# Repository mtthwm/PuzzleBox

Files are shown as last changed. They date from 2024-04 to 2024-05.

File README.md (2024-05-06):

# About

## Description
This is a project built for our ECE 5780 (Embedded Systems) final project. We built a puzzle box that requires the user to interact with it in novel ways to unlock and reveal the prize inside. 

### Puzzle 1: Knock and Response 

The buzzer plays a common knock rhythm, and the user must respond to finish the rhythm. 
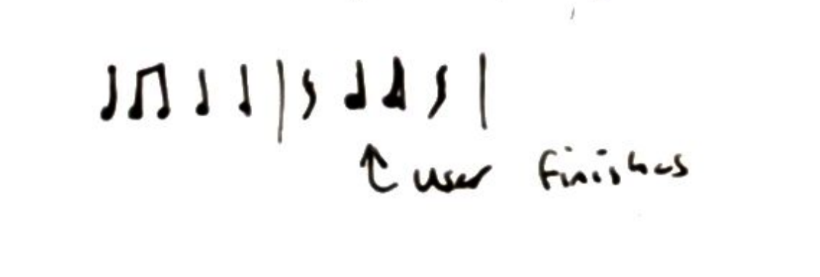
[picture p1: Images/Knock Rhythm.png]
Image of the common door knock rhythm that everyone knows


### Puzzle 2:  

Led on sides of the box lights up, rotate the whole box so the LED points down. Repeat 3 times with a random side each time. 

### Puzzle 3: 

Using multiple photoresistors, a sequence of holes needs to either be lit or covered.  

### Puzzle Completion: 

Using a servo, unlock the box for opening. Puzzle restarts on close. 

## Collaborators
- Matthew Morales
- Daniel Reyna
- Casey Wolfe
- Griffin Rodgers

# Project Setup Instructions

## Assembly
1. Print the box and lid using the provided STL files. Our original design was slightly off, which required us to drill into the box to make room for the servo locking mechanism.
2. Glue LEDs and photoresistors into the holes in the side. Each LED has a 220 Ohm resistor in series, and each photoresistor is part of a voltage divider with a 10k Ohm resistor. Make sure to match up the LEDs which correspond to the photoresistors.
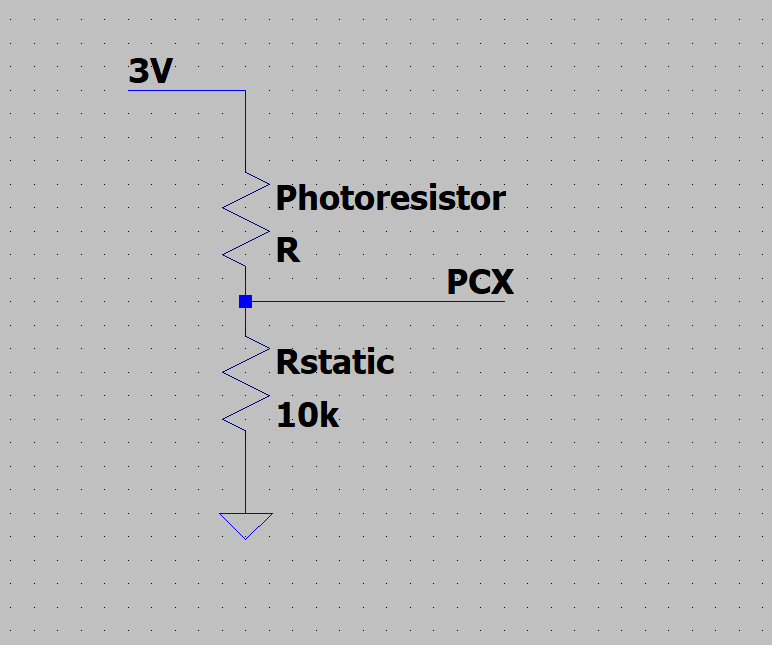
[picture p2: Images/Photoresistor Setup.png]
Photoresistor voltage divider example

3. Attach the piezo resistor to the underside of the lid using hot glue. This seems to cushion the vibrations picked up by the piezo resistor enough to avoid large voltage spikes. As a result, we didn't connect it to a voltage divider.
4. Once the piezo sensor is attached, you may need to use usart to display the values in order to pick a proper voltage threshold for the piezo sensor. It seemed the voltage generated by these sensors varied significantly
5. Open the project in Keil uVision, compile the project, and flash it to your STM32F0 Discovery Kit Board.

## Pins
- I2C:  
  - SCL: PB10 
  - SDA: PB11 

- UART (debug):  
  - TX: PC10 
  - RX: PC11 

- ADC: PC0-3
  - Piezo: PC0 
  - Photoresistors PC3,4,5

- Buzzer: PB5 

- Box-Side LEDs 
   - PA0 -- Top LED 
   - PA1 – Base LED 
   - PA8 – Front LED 
   - PA9 – Back LED 
   - PA10 – Left Side LED
   - PA15 – Right Side LED	 

- Servo: PB3 

# Puzzle Box - Hints & Solution
## Hints (for fun)
Given: Each stage completion (3 total) will be associated with a victory tune, as well as a brief LED light show.

### Hint (1): 
The box plays a near complete tune, no question there; make haste and knock to – to finish it is the burden you bear.

### Hint (2): 
The box has many sides, it is of no surprise; what does the light confide? Rotate to abide?

### Hint(3.1): 
Your final steps await, the box’s prize is in your fate; darkness – you think – may be your friend, but its enemy may tend.

### Hint(3.2):
Thus far you found your tool, you’re on the path; but have you checked if there is a dual?

## Solution
(1) A buzzer plays an incomplete tune. Wait until it finishes. Knock once, wait half a second then knock again. A victory tune will be played
(2) An LED will indicate which side needs to be up. First is bottom, then right side, then top. A victory tune will be played
(3) LEDs will indicate which side’s photoresistor must be interacted with. You must shine a light to the bottom side photoresistor first, followed by the back, followed by both back and top (2 lights required, or 1 shining on both directly)
(4) An extended victory tune is played, followed by a LED lightshow. The box servo unlocks shortly after and can be opened.

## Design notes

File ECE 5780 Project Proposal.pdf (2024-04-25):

## Group Members

Casey Wolfe
Matthew Morales
Griffin Rodgers
Daniel Reyna

## Project Description

We will build a puzzle box that requires the user to interact with it in novel ways to unlock and reveal the prize inside. The box will have a GPS, a knock detector piezo sensor, a gyroscope, and a photo resistor hidden inside. Markings on the outside of the box will guide the user to interact with the various inputs to solve puzzles. A buzzer inside the box and LED indicators will provide active feedback to the user. There will be four puzzles, once all the puzzles are solved a solenoid will unlock the box from inside.
Puzzle ideas include tilting the box to a certain orientation, moving the box a specific distance, knocking on the box in a specific pattern, and shining a light through a small hole in the box.

## Motivation

We chose this project idea because it seemed like a very flexible way to get experience with a lot of different sensors and actuators. We also thought it would be a creative and unique concept to explore, combining both embedded systems and game design. We have selected unconventional user interfaces that use technology to challenge the user to think creatively to solve puzzles.

## Block Diagram

## Hardware Components

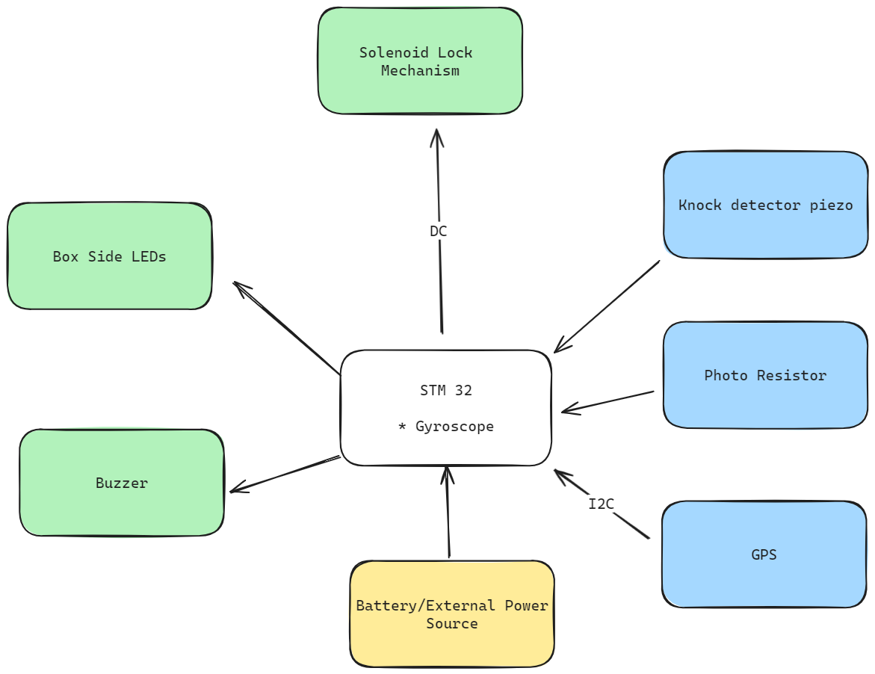
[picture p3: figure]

## Software State Machine

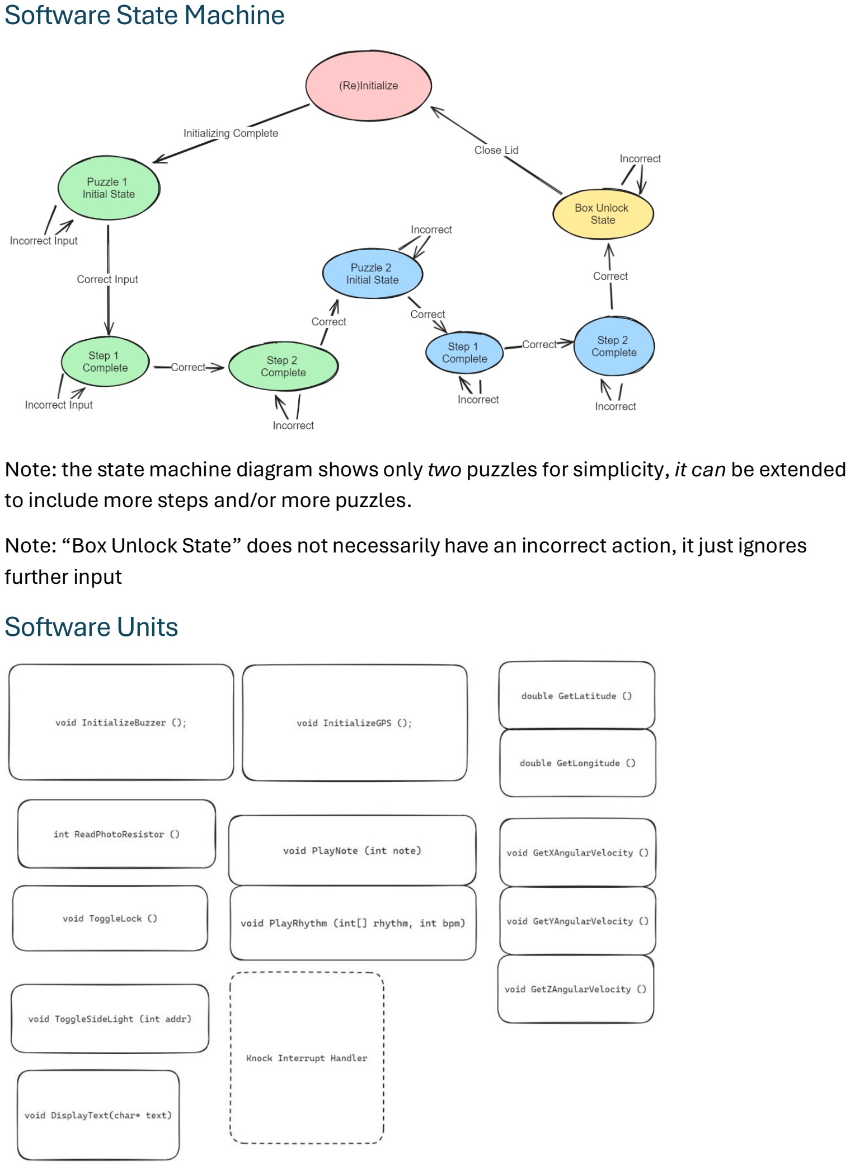
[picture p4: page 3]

Note: the state machine diagram shows only two puzzles for simplicity, it can be extended to include more steps and/or more puzzles.
Note: “Box Unlock State” does not necessarily have an incorrect action, it just ignores further input

## Software Units

## Milestones

## Milestone 1

Primary Goal: Communication with the piezo sensor, and buzzer.

- Buzzer can play a rhythm
- Main loop switch statement for state machine
Secondary Goals:
- Piezo sensor can detect a pattern of taps
- Obtain parts
- Puzzles designed

## Milestone 2

Primary Goal: Communication with accelerometer for rotation puzzle. Main state machine architecture complete.

- Can decide which side is facing down
- We can easily address the side LEDs
- We can randomly turn on an LED Secondary Goals:
- Box design complete
Tasks:
- Piezo
- Detect knocks
- Store knock history
- Buzzer
- Function to play tone for certain time
- Play sequence of tones
- Accelerometer
- Read I2C
- Function to return which side is down

o

## Milestone 3

Primary Goal: Measurement of the photoresistors

- We can detect light/dark/ambient state on each photo resistors
- We can communicate with 5 Photoresistors
- Can rapidly flash LEDs on one side
Secondary Goals:
- Box assembled

## Milestone 4

Primary Goal: Communication with servo to open the lid; Finished puzzle box.

- Can send a lock/unlock signal to the lock mechanism
- Play a fanfare on open
- Can transition to back to play state
Secondary Goals:
- Fully test the project
- Debug/fix any software issues
- Add features if time permits

## Discussion of Risk

One of the biggest risks we have identified with this mini project is the physical design aspects of the puzzle box. We have access to a 3D printer for rapid prototyping of the box, however none of us are particularly experienced in 3D modeling. This risk will be mitigated by dedicating time to learning basic 3D modeling in CAD software.
Another risk is that our team does not include an Electrical Engineer, so we may struggle more with some of the hardware design/implementation aspects of the project. This risk is partially mitigated through having two Computer Engineers on the team; however, Computer Engineers are not as experienced in hardware as an Electrical Engineer would be.

## Pins

I2C:
SCL: B10
SDA: B11
UART (debug):
TX: PC10
RX: PC11
ADC: A pins
Piezo: C0
Photoresistors: PA1-5 and PA7 DMA BUFFER:
PIEZO - [0]
Top Resistor - [1]
Bottom Resistor - [2]
Back Resistor - [3]
Buzzer: PB5

Box-Side LEDs

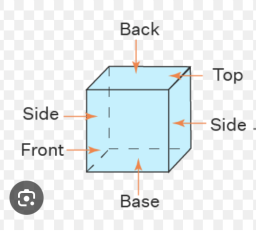
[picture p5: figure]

PA0 -- Top LED
PA1 – Base LED
PA8 – Front LED
PA9 – Back LED

PA10 – Left Side LED
PA15 – Right Side LED
Servo: PB3

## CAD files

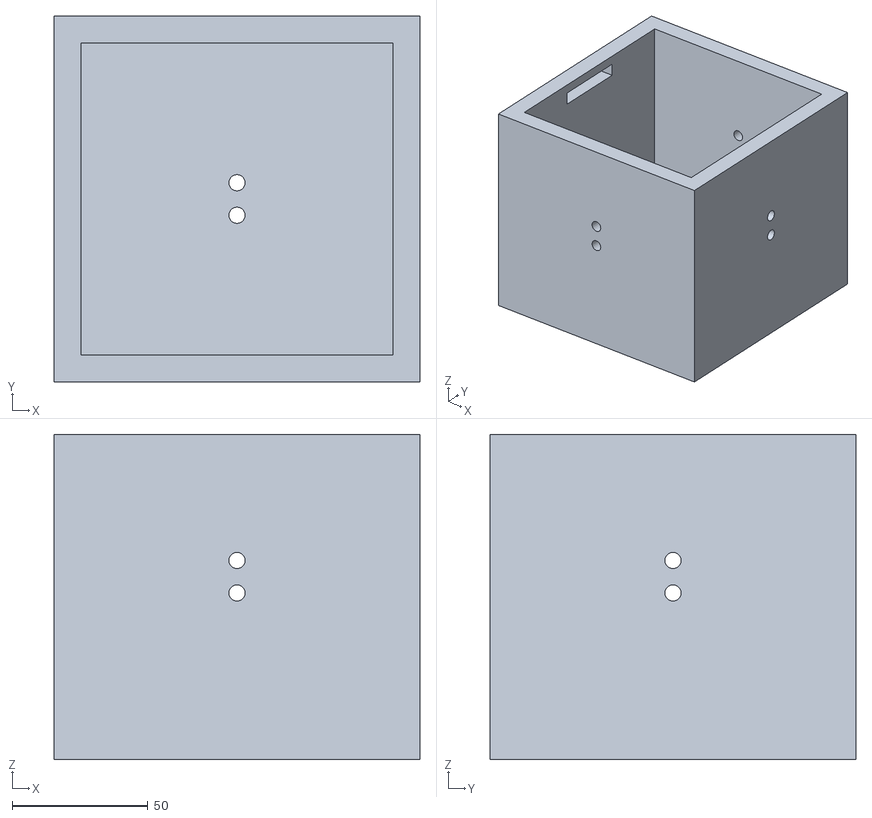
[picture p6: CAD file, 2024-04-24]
Puzzle Box.stl
135.0 x 135.0 x 120.0

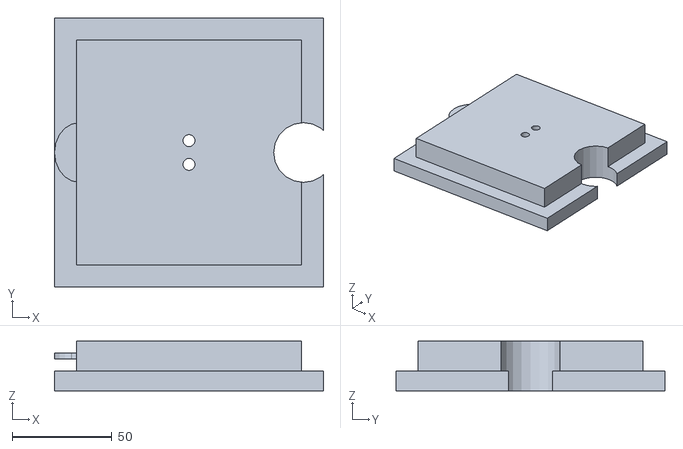
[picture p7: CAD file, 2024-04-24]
Puzzle Box Lid.stl
135.0 x 135.0 x 25.0

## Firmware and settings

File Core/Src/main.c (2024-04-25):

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
/* Includes ------------------------------------------------------------------*/
#include "main.h"

/* USER CODE BEGIN Includes */

#include "servo.h"
#include "accel.h"
#include "adc.h"

/* USER CODE END Includes */

/* USER CODE BEGIN PV */

// Contains values for 3 photoresistors and PIEZO
// [0] contains piezo
// [1] is the top photoresistor
// [2] is the bottom photoresistor
// [3] is the back photoresistor

/* USER CODE END PV */

void SystemClock_Config(void);
/* USER CODE BEGIN 0 */


void victoryBoxLEDs();
void unlock ();

////////////////// UART ////////////////////////////////////////////////////////////////////////
#define RX_BUFF_SIZE 2

static char rx_chars[RX_BUFF_SIZE];
static int rx_i = 0;

/**
	* @brief Configures USART with PC10=RX, PC11=TX
	*/
void config_usart (uint32_t baudrate) {
	// Set the mode of the GPIO pins to use an alternate function
	GPIOC->MODER &= ~(GPIO_MODER_MODER10_Msk);
	GPIOC->MODER &= ~(GPIO_MODER_MODER11_Msk);
	GPIOC->MODER |= (2 << GPIO_MODER_MODER10_Pos);
	GPIOC->MODER |= (2 << GPIO_MODER_MODER11_Pos);

	
	// Set GPIO Pins PC10 and PC11 to use alternate function AF1: USART3
	GPIOC->AFR[1] &= ~GPIO_AFRH_AFSEL10_Msk;
	GPIOC->AFR[1] |= (GPIO_AF1_USART3 << GPIO_AFRH_AFSEL10_Pos); // TX
	GPIOC->AFR[1] &= ~GPIO_AFRH_AFSEL11_Msk;
	GPIOC->AFR[1] |= (GPIO_AF1_USART3 << GPIO_AFRH_AFSEL11_Pos); // RX
	
	// Enable USART TX and RX
	USART3->CR1 |= USART_CR1_TE;
	USART3->CR1 |= USART_CR1_RE;
	
	// Set the USART Baud Rate to 115200 bit/sec
	USART3->BRR = (HAL_RCC_GetHCLKFreq()/baudrate);
	
	// Enable RXNE Interrupt
	USART3->CR1 |= USART_CR1_RXNEIE;
	
	// Configure interrupt handler for RXNE
	NVIC_EnableIRQ(USART3_4_IRQn);
	
	// Configure interrupt priorities
	NVIC_SetPriority(USART3_4_IRQn, 1);
	NVIC_SetPriority(SysTick_IRQn, 0);
	
	// Enable USART. Config vars become readonly!
	USART3->CR1 |= USART_CR1_UE;
}
void usart_transmit_char (char c) {
	int wait = 1;
	while (wait) {
		if ((USART3->ISR & USART_ISR_TXE_Msk)) {
			wait = 0;
		}
	} // Wait until the register is empty for transmission

	USART3->TDR = c;
}
void usart_transmit_str (char* s) {
	int i = 0;
	do {
		usart_transmit_char(s[i]);
		i++;
	} while (s[i] != '\0');
	
	usart_transmit_char('\0');
}
void usart_transmit_int (uint16_t num) {
	char buff[16] = {0,0,0,0,0,0,0,0,0,0,0,0,0,0,0,0};
	int8_t i = 0;
	while (num != 0 && i < 8) {
		buff[i] = (num % 10) + 48;
		num = num / 10;
		i++;
	}
	
	for (int8_t i = 7; i > -1; i--) {
		usart_transmit_char(buff[i]);
	}
	usart_transmit_char('\r');
	usart_transmit_char('\n');
}
void USART3_4_IRQHandler () {
	char received = USART3->RDR;
	if (rx_i >= RX_BUFF_SIZE || rx_i < 0) {
		return;
	}
	rx_chars[rx_i] = received;
	rx_i++;
}
////////////////////////////////////////////////////////////////////////////////////////

void playKnockPrompt();

//////////////////////////////
//// BOX SIDE-LED CONFIG /////
//////////////////////////////
void config_sideLEDs()
{
	
	GPIO_InitTypeDef initStr = {GPIO_PIN_0 | GPIO_PIN_1 | GPIO_PIN_8 | GPIO_PIN_9 | GPIO_PIN_10 | GPIO_PIN_15,
	GPIO_MODE_OUTPUT_PP,
	GPIO_SPEED_FREQ_LOW,
	GPIO_NOPULL};
	
	HAL_GPIO_Init(GPIOA, &initStr); 
//	// Clear state of Moder reg for pins [8-12], [15] (00)
//	GPIOA->MODER &= ~((1 << 31) | (1 << 30));
//	GPIOA->MODER &= ~((1 << 24) | (1 << 22) | (1 << 20) | (1 << 18) | (1 << 16));

//	// Pins [8-12], [15] to General Purpose Output (01)
//	GPIOA->MODER |= (1 << 30);
//	GPIOA->MODER |= (1 << 24) | (1 << 22) | (1 << 20) | (1 << 18) | (1 << 16);


//	// Pins [8-12], [15] to Output push-pull (0)
//	GPIOA->OTYPER &= ~((1 << 15) | (1 << 12) | (1 << 11) | (1 << 10) | (1 << 9) | (1 << 8));

//	// Pins [8-12], [15] to Low Speed (x0)
//	GPIOA->OSPEEDR &= ~((1 << 30) | (1 << 24) | (1 << 22) | (1 << 20) | (1 << 18) | (1 << 16));

//	// Pins [8-12], [15] to "No Pull-Up, Pull-Down" (00)
//	GPIOA->PUPDR &= ~((1 << 31) | (1 << 30)); // pin 15
//	GPIOA->PUPDR &= ~((1 << 25) | (1 << 24)); // 12
//	GPIOA->PUPDR &= ~((1 << 23) | (1 << 22)); // 11
//	GPIOA->PUPDR &= ~((1 << 21) | (1 << 20)); // 10
//	GPIOA->PUPDR &= ~((1 << 19) |(1 << 18)); // 9
//	GPIOA->PUPDR &= ~((1 << 17) | (1 << 16)); // 8

//	 // Pins [8-12], [15] set to OFF (0)
//	GPIOA->ODR &= ~((1 << 15) | (1 << 12) | (1 << 11) | (1 << 10) | (1 << 9) | (1 << 8));
}

// Pin PA8
void toggle_LED_front(char mode){
	switch(mode){
		case 0:
			GPIOA->ODR &= ~(1 << 8);
			break;
		case 1:
			GPIOA->ODR |= (1 << 8);
			break;
		case 2:
			GPIOA->ODR ^= (1 << 8);
			break;
	}
}

// Pin PA9
void toggle_LED_back(char mode){
	switch(mode){
		case 0:
			GPIOA->ODR &= ~(1 << 9);
			break;
		case 1:
			GPIOA->ODR |= (1 << 9);
			break;
		case 2:
			GPIOA->ODR ^= (1 << 9);
			break;
	}
}

// Pin PA0
void toggle_LED_top(char mode){
	switch(mode){
		case 0:
			GPIOA->ODR &= ~(1 << 0);
			break;
		case 1:
			GPIOA->ODR |= (1 << 0);
			break;
		case 2:
			GPIOA->ODR ^= (1 << 0);
			break;
	}
}

// Pin PA1
void toggle_LED_bottom(char mode){
	switch(mode){
		case 0:
			GPIOA->ODR &= ~(1 << 1);
			break;
		case 1:
			GPIOA->ODR |= (1 << 1);
			break;
		case 2:
			GPIOA->ODR ^= (1 << 1);
			break;
	}
}

// Pin PA10
void toggle_LED_left(char mode){
	switch(mode){
		case 0:
			GPIOA->ODR &= ~(1 << 10);
			break;
		case 1:
			GPIOA->ODR |= (1 << 10);
			break;
		case 2:
			GPIOA->ODR ^= (1 << 10);
			break;
	}
}

// Pin PA15
void toggle_LED_right(char mode){
	switch(mode){
		case 0:
			GPIOA->ODR &= ~(1 << 15);
			break;
		case 1:
			GPIOA->ODR |= (1 << 15);
			break;
		case 2:
			GPIOA->ODR ^= (1 << 15);
			break;
	}
}

/**
 * Configures all LEDs based on input.
 * @param mode '0' = ALL OFF | '1' = ALL ON | '2' = ALL INVERT
 */
void toggle_LED_all(char mode){
	switch(mode){
		case 0:
			toggle_LED_top(0);
			toggle_LED_bottom(0);
			toggle_LED_front(0);
			toggle_LED_back(0);
			toggle_LED_left(0);
			toggle_LED_right(0);
			break;
		case 1:
			toggle_LED_top(1);
			toggle_LED_bottom(1);
			toggle_LED_front(1);
			toggle_LED_back(1);
			toggle_LED_left(1);
			toggle_LED_right(1);
			break;
		case 2:
			toggle_LED_top(2);
			toggle_LED_bottom(2);
			toggle_LED_front(2);
			toggle_LED_back(2);
			toggle_LED_left(2);
			toggle_LED_right(2);
			break;
	}
}

//////////////////////////////////////////////

//////////////////////////
//// BOARD LED CONFIG ////
//////////////////////////
void config_red () {
	GPIOC->MODER &= ~(GPIO_MODER_MODER6_Msk);
	GPIOC->MODER |= GPIO_MODER_MODER6_0;
	GPIOC->OTYPER &= ~(GPIO_OTYPER_OT_6);
	GPIOC->OSPEEDR &= ~(GPIO_OSPEEDR_OSPEEDR6_Msk);
	GPIOC->PUPDR &= ~(GPIO_PUPDR_PUPDR6_Msk);
	GPIOC->ODR &= ~GPIO_ODR_6;
}
void toggle_red (char mode) {
	switch (mode) {
		case 2:
			GPIOC->ODR ^= GPIO_ODR_6;
			break;
		case 1:
			GPIOC->ODR |= GPIO_ODR_6;
			break;
		case 0:
			GPIOC->ODR &= ~GPIO_ODR_6;
			break;
	}
}
void config_blue () {
	GPIOC->MODER &= ~(GPIO_MODER_MODER7_Msk);
	GPIOC->MODER |= GPIO_MODER_MODER7_0;
	GPIOC->OTYPER &= ~(GPIO_OTYPER_OT_7);
	GPIOC->OSPEEDR &= ~(GPIO_OSPEEDR_OSPEEDR7_Msk);
	GPIOC->PUPDR &= ~(GPIO_PUPDR_PUPDR7_Msk);
	GPIOC->ODR &= ~GPIO_ODR_7;
}
void toggle_blue (char mode) {
	switch (mode) {
		case 2:
			GPIOC->ODR ^= GPIO_ODR_7;
			break;
		case 1:
			GPIOC->ODR |= GPIO_ODR_7;
			break;
		case 0:
			GPIOC->ODR &= ~GPIO_ODR_7;
			break;
	}
}
void config_orange () {
	GPIOC->MODER &= ~(GPIO_MODER_MODER8_Msk);
	GPIOC->MODER |= GPIO_MODER_MODER8_0;
	GPIOC->OTYPER &= ~(GPIO_OTYPER_OT_8);
	GPIOC->OSPEEDR &= ~(GPIO_OSPEEDR_OSPEEDR8_Msk);
	GPIOC->PUPDR &= ~(GPIO_PUPDR_PUPDR8_Msk);
	GPIOC->ODR &= ~GPIO_ODR_8;
}
void toggle_orange (char mode) {
	switch (mode) {
		case 2:
			GPIOC->ODR ^= GPIO_ODR_8;
			break;
		case 1:
			GPIOC->ODR |= GPIO_ODR_8;
			break;
		case 0:
			GPIOC->ODR &= ~GPIO_ODR_8;
			break;
	}
}
void config_green () {
	GPIOC->MODER &= ~(GPIO_MODER_MODER9_Msk);
	GPIOC->MODER |= GPIO_MODER_MODER9_0;
	GPIOC->OTYPER &= ~(GPIO_OTYPER_OT_9);
	GPIOC->OSPEEDR &= ~(GPIO_OSPEEDR_OSPEEDR9_Msk);
	GPIOC->PUPDR &= ~(GPIO_PUPDR_PUPDR9_Msk);
	GPIOC->ODR &= ~GPIO_ODR_9;
}
void toggle_green (char mode) {
	switch (mode) {
		case 2:
			GPIOC->ODR ^= GPIO_ODR_9;
			break;
		case 1:
			GPIOC->ODR |= GPIO_ODR_9;
			break;
		case 0:
			GPIOC->ODR &= ~GPIO_ODR_9;
			break;
	}
}
/////////////////////////////////////////////////

#define KNOCK_THRESH_HI 3500

////////////////////////////////////
///// PHOTORESISTOR GET() functions
/////////////////////////////////////
uint16_t getResistorTop(){
	return dmaUtil_buffer[1];
}

uint16_t getResistorBottom(){
	return dmaUtil_buffer[2];
}

uint16_t getResistorBack(){
	return dmaUtil_buffer[3];
}
////////////////////////////////////////////

static volatile uint16_t knockCount = 0;
static uint32_t lastKnockTransmissionTime = 0;

uint32_t firstTime = 0;
uint32_t secondTime = 0;

/**
 * Non-blocking function to handle Puzzle 1 - knock detection.
 * Returns true if the puzzle is completed, false otherwise
 *
 * @return 1 if the puzzle is completed, 0 otherwise
 */
int getKnockTiming() {
	// Function GLOBALS
	const uint32_t INPUT_DELAY = 500; // Delay between the start of puzzle, and accepting user input
	const uint32_t MIN_DELAY_BETWEEN = 400; // MIN time allowed that we will accept the first knock
	const uint32_t MAX_DELAY_BETWEEN = 1000; // MAX time allowed that we will accept 2nd knock
	const uint32_t DELAY_BEFORE_REPLAYING = 10000;
	
	uint32_t elapsedTime = 0;
	
	// Function Non-blocking sentinels (track if something has occured or not)
	static uint32_t promptDelayDone = 0; // Non-blocking way to track if delay has elapsed
	static uint32_t promptTunePlayed = 0; // Track if the buzzer has played the puzzle tune
	static uint32_t firstTimerTimed = 0; // Track if the first knock time has been recorded
	static uint32_t secondTimerTimed = 0; // Track if the second knock time has been recorded
		
	// Puzzle tune plays ONCE, disabled afterwards.
	if (!promptTunePlayed){
		firstTime = HAL_GetTick();
		promptTunePlayed = 1;
		playKnockPrompt();
	}
	
	elapsedTime = HAL_GetTick() - firstTime;
	
	if (!promptDelayDone) {
		// Wait a certain amount of time before taking user-input (knocks)
		if (elapsedTime >= INPUT_DELAY) {
			knockCount = 0;
			promptDelayDone = 1;
		} else {
			return 0;
		}
	}
	
	char fail = 0;
	
	// How long has it been since we last prompted the user?
	if (elapsedTime >= DELAY_BEFORE_REPLAYING) {
		fail = 1; // Timed out before we got two knocks. Re-prompt the user
	}
	
	if (secondTime != 0) { 
		// The second knock was received!
		uint32_t delayBetween = secondTime - firstTime;
		if ((delayBetween < MIN_DELAY_BETWEEN) || (delayBetween > MAX_DELAY_BETWEEN)) {
			fail = 1; // Timing was off. Re-prompt the user
		} else {
			return 1; // Timing was good!
		}
	}
	
	if (fail)
	{
		knockCount = 0;
		firstTime = 0;
		secondTime = 0;
		promptDelayDone = 0;
		promptTunePlayed = 0;
		firstTimerTimed = 0;
		secondTimerTimed = 0;
		toggle_orange(0);
	}
	
	toggle_orange(1);
	
	// PUZZLE PHASE - After buzzer plays and a short delay
	switch(knockCount){
		case 0:
			break;
		
		// FIRST KNOCK - Simply log the timestamp of first knock
		case 1:
			if (!firstTimerTimed){
				firstTime = HAL_GetTick();
				firstTimerTimed = 1;
			}
			break;
		
		// WAIT PHASE -- wait for 2nd knock, or soft-reset puzzle if waiting too long
		case 2:		
			if (!secondTimerTimed) {
				secondTime = HAL_GetTick();
				secondTimerTimed = 1;
			}
			break;
	};
				
	return 0;
}

enum PuzzleStateType {
	Puzzle1,
	Puzzle2,
	Puzzle3,
	GameEnd
};

void handleKnocks () {
	static uint8_t debouncer = 0;
	debouncer <<= 1;
	
	if (dmaUtil_buffer[0] > KNOCK_THRESH_HI) {
		debouncer |= 1;
	}
	
	if (debouncer == 0x1) {
		knockCount++;
	}
}

// returns true when puzzle is solved
int doPuzzle1() {
	handleKnocks();
	return getKnockTiming();
}

/**
 * Uses the accelerometer orientation to check if the user
 * (1) flips the box upside-down
 * (2) places the box on its right side
 * (3) Re-orients the box upright (default starting orientation)
 *
 * @return 1 if puzzle is completed, 0 otherwise


notes:
tilting back towards up ==> Y_POS
tilting right towards top ==> X_POS
front side up ==> Y_NEG
 */
int doPuzzle2() {
	int orientation = accelReadAxis();
	static uint16_t puzzleStage = 0;
	switch(puzzleStage){
		case 0:
			puzzleStage = 1;
			toggle_LED_bottom(1);
			break;
		// Wait until box is upside down
		case 1:
			if (orientation == Z_NEG){
				puzzleStage = 2;
				toggle_LED_bottom(0);
				toggle_LED_right(1);
			}
			break;
		// Wait until box is on its right side
		case 2:
			if (orientation == X_POS){
				puzzleStage = 3;
				toggle_LED_right(0);
				toggle_LED_top(1);
			}
			break;
		// Wait until box is upright
		case 3:
			if (orientation == Z_POS){
				toggle_LED_top(0);
				return 1;
			}
			break;
		
		// Error, reset puzzle back to stage 0
		default:
			puzzleStage = 0;
			return 0;
	}
	return 0;
}

/**
 * Puzzle 3 - Photoresistor Checks
 * Puzzle will include lighting the photoresistors
 * Each photoresistor will be associated with an LED
 * A lit LED indicates the hole will need to be lit up
 *
 * This function will sequentially check if
 * (1) The top photoresistor is lit up
 * (2) The bottom photoresistor is lit up
 * (3) Both the top and front photoresistors are lit (small challenge)
 */
int doPuzzle3() {
	const uint16_t LIGHT_THRESHOLD = 3700;
	static uint16_t puzzleStage = 0;

	switch(puzzleStage){
		case 0:
			toggle_LED_top(1);
			puzzleStage = 1;
			break;

		// Light TOP resistor
		case 1:
			if (getResistorTop() > LIGHT_THRESHOLD){
				toggle_LED_top(0);
				toggle_LED_bottom(1);
				puzzleStage = 2;
			}
			break;
		
		// Light BOTTOM resistor
		case 2:
			if(getResistorBottom() > LIGHT_THRESHOLD){
				toggle_LED_bottom(0);
				toggle_LED_back(1);
				toggle_LED_top(1);
				puzzleStage = 3;
			}
			break;

		// Light TOP and BACK resistor
		case 3:
			if(getResistorTop() > LIGHT_THRESHOLD && getResistorBack() > LIGHT_THRESHOLD){
				toggle_LED_top(0);
				toggle_LED_back(0);
				return 1;
			}
			break;
	}
	return 0;
}

/**
 * Ends the game by flashing box LEDs, then unlocking the servo-lock
 * This function never exits. The system must reset.
 */
void doGameEnd() {
	victoryBoxLEDs();
	unlock(); // TODO: Is this the correct servo angle for "unlock"?
	while (1){
		toggle_blue(2);
		toggle_green(2);
		toggle_orange(2);
		toggle_red(2);
		HAL_Delay(250);
	}
}

void pwmInit() {
	
	__HAL_RCC_GPIOB_CLK_ENABLE();
	__HAL_RCC_TIM3_CLK_ENABLE();
	
	GPIO_InitTypeDef initStrPWM = {GPIO_PIN_5,
	GPIO_MODE_AF_PP,
	GPIO_SPEED_FREQ_LOW,
	GPIO_NOPULL,
	GPIO_AF1_TIM3};
	
	
	HAL_GPIO_Init(GPIOB, &initStrPWM);
	
	TIM3 -> PSC = 2; // Set PSC to divide clock by 250 (equivalent to 1/32 of a ms)
	TIM3 -> ARR = 100; // 40 * 1/32 = 1.25 ms (aka 800 hz)
	
	TIM3 -> CCMR1 &= ~TIM_CCMR1_CC2S; // Clear CC2S aka set CC1S to 0b0000
	TIM3 -> CCMR1 |= TIM_CCMR1_OC2M; // Set OC2M to PWM Output 2 mode (0b111)
	TIM3 -> CCMR1 |= TIM_CCMR1_OC2PE; // Preload enable channel 2
	TIM3 -> CCER |= TIM_CCER_CC2E; // Enable capture/compare for channel 2
	
	TIM3 -> CCR2 = 2; // Set duty cycle to 20% (of ARR)
		
}

void playTone(uint16_t freq) {
	uint16_t arr = 8000000 / (3 * freq);
	TIM3->ARR = arr;
	TIM3->CCR2 = arr / 2;
}

void playTune(uint16_t *frequencies, uint16_t *durations, uint16_t length) {
	for (int i = 0; i < length; i++) {
		if (frequencies[i] == 0) {
			TIM3->CR1 &= ~TIM_CR1_CEN;  // stop the timer
		}
		else {
			TIM3->CR1 |= TIM_CR1_CEN;  // start the timer
			playTone(frequencies[i]);
		}
		
		HAL_Delay(durations[i]);
	}
	TIM3->CR1 &= ~TIM_CR1_CEN;  // stop the timer after the tune completes
}

void playKnockPrompt () {
	uint16_t frequencies[10] = {196, 0, 146, 0, 146, 0, 164, 0, 146};
	uint16_t durations[10] = {500, 10, 250, 10, 250, 10, 250, 260, 500};

	playTune(frequencies, durations, 10);
}

void playFanfare(int num) {
	uint16_t chord1[] = {261, 329, 392, 523};
	uint16_t chord2[] = {294, 370, 440, 587};
	uint16_t chord3[] = {330, 415, 494, 831, 659, 831, 988};
	uint16_t durations[] = {200, 200, 200, 600};
	uint16_t durations2[] = {200, 200, 200, 200, 200, 200, 600};
	
	switch (num) {
		case 1:
			playTune(chord1, durations, 4);
			break;
		
		case 2:
			playTune(chord2, durations, 4);
			break;
		
		case 3:
			playTune(chord3, durations2, 7);
			break;
	}
	
}

/**
 * Function that flashes ALL box LEDs 5 times
 * Intended to indicate progress in the puzzle.
 * Function is somewhat blokcing, uses HAL_Delay
 */
void flashBoxLEDs(){
	toggle_LED_all(0);
	for(int i = 0; i < 6; i++){
		toggle_LED_all(2);
		HAL_Delay(50);
	}
}

/**
 * Used to indicate something major occuring (the puzzle box being solved)
 * Function is somewhat blocking, using HAL_Delay
 */
void victoryBoxLEDs(){
	toggle_LED_all(0);
	for (int i = 0; i < 6; i++){
		// All on sequentially
		toggle_LED_front(1);
		HAL_Delay(50);

		toggle_LED_left(1);
		HAL_Delay(50);

		toggle_LED_back(1);
		HAL_Delay(50);

		toggle_LED_right(1);
		HAL_Delay(50);

		// All off sequentially
		toggle_LED_front(0);
		HAL_Delay(50);

		toggle_LED_left(0);
		HAL_Delay(50);

		toggle_LED_back(0);
		HAL_Delay(50);

		toggle_LED_right(0);
		HAL_Delay(50);
	}
	for(int i = 0; i < 6; i++){
		toggle_LED_all(2);
		HAL_Delay(50);
	}
	toggle_LED_all(1);
}

void config_knock_adc () {
	adcUtil_setup(ADC1, adcUtil_12bit);
	
	// Set PC0 to analog mode
	GPIOC->MODER |= 3 << GPIO_MODER_MODER0_Pos;
	GPIOC->MODER |= 3 << GPIO_MODER_MODER3_Pos;
	GPIOC->MODER |= 3 << GPIO_MODER_MODER4_Pos;
	GPIOC->MODER |= 3 << GPIO_MODER_MODER5_Pos;
	
	GPIOC->PUPDR &= ~GPIO_PUPDR_PUPDR0;
	GPIOC->PUPDR &= ~GPIO_PUPDR_PUPDR1;
	GPIOC->PUPDR &= ~GPIO_PUPDR_PUPDR2;
	GPIOC->PUPDR &= ~GPIO_PUPDR_PUPDR3;

	adcUtil_enableChannel(ADC1, 10);
	adcUtil_enableChannel(ADC1, 13);
	adcUtil_enableChannel(ADC1, 14);
	adcUtil_enableChannel(ADC1, 15);

	
	adcUtil_calibrate(ADC1, 1);	
}

void unlock () {
	servoUtil_setServo(8);
}

void lock () {
	servoUtil_setServo(0);
}

/* USER CODE END 0 */

/**
  * @brief  The application entry point.
  * @retval int
  */
int main(void)
{
	
	
  /* MCU Configuration--------------------------------------------------------*/

  /* Reset of all peripherals, Initializes the Flash interface and the Systick. */
  HAL_Init();
	
	/* Configure the system clock */
  SystemClock_Config();

  /* USER CODE BEGIN Init */
	
	// Enable the RCC clocks
	__HAL_RCC_USART3_CLK_ENABLE();
	__HAL_RCC_GPIOA_CLK_ENABLE();
	__HAL_RCC_GPIOB_CLK_ENABLE();
	__HAL_RCC_GPIOC_CLK_ENABLE();
	__HAL_RCC_TIM2_CLK_ENABLE();
	
	config_red();
	config_green();
	config_blue();
	config_orange();
	config_sideLEDs(); // additional LED's on pins PA8-PA12, and PA15
	
	
	
	pwmInit();
	
	dmaUtil_configChannel();
	config_knock_adc();
	servoUtil_configServo();
	config_usart(115200);

	usart_transmit_str("USART READY!\n");
	
	HAL_Delay(1000);

	int8_t initVal = initAccelerometer();
	if(initVal == 1) {
		while (1) {
			toggle_red(2);
			HAL_Delay(250);
		}
	}
	else if(initVal == 2) {
		while (1) {
			toggle_orange(2);
			HAL_Delay(250);
		}
	}
	
  /* USER CODE END Init */

  

  /* Initialize all configured peripherals */
  /* USER CODE BEGIN 2 */

	/*
	if(!accelSetupRegisters()) {
		toggle_red(1);
		while(1);
	}
	*/
	
	accelSetupRegisters();
	
	usart_transmit_str("Config done!\n\r");
	toggle_blue(1);
	HAL_Delay(1000);
	toggle_blue(0);
	
	HAL_Delay(5000);
	lock(); // Lock the servo on start after 5 seconds
	
	enum PuzzleStateType mainState = Puzzle1;
	
	//toggle_LED_all(1);
	//victoryBoxLEDs();
	//while(1);
	

  /* USER CODE END 2 */

  /* Infinite loop */
  /* USER CODE BEGIN WHILE */
  while (1)
  {	
		/*
		if (HAL_GetTick() - lastKnockTransmissionTime >= 500) {
			usart_transmit_int(knockCount);
			lastKnockTransmissionTime = HAL_GetTick();
		}
		*/

	/*	
	usart_transmit_str("ADC OVR: ");
	usart_transmit_int(ADC1->ISR & ADC_ISR_OVR);
	usart_transmit_str("Channel 1: ");
	usart_transmit_int(dmaUtil_buffer[0]);
	usart_transmit_str("Channel 2: ");
	usart_transmit_int(dmaUtil_buffer[1]);
	usart_transmit_str("Channel 3: ");
	usart_transmit_int(dmaUtil_buffer[2]);
	usart_transmit_str("Channel 4: ");
	usart_transmit_int(dmaUtil_buffer[3]);*/
	//usart_transmit_int(ADC1->DR);
	//HAL_Delay(100);
	//continue; // SKIP SWITCH HERE FOR DEBUG
  

	switch (mainState) {
		case Puzzle1:
			if (doPuzzle1()) {
				playFanfare(1);
				flashBoxLEDs();
				mainState = Puzzle2;
			}
			break;
		
		case Puzzle2:
			toggle_blue(1);	
			if (doPuzzle2()) {
				playFanfare(2);
				flashBoxLEDs();
				mainState = Puzzle3;
			}
			break;

		case Puzzle3:
			if (doPuzzle3()) {
				playFanfare(3);
				flashBoxLEDs();
				mainState = GameEnd;
			}
			break;
			
		case GameEnd:
			doGameEnd();
			break;
		}
	
		HAL_Delay(1);
  }
  /* USER CODE END WHILE */

}

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


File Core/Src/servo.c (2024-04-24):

#include "servo.h"

void servoUtil_configServo() {
	GPIO_InitTypeDef initStrPWM = {GPIO_PIN_3,
	GPIO_MODE_AF_PP,
	GPIO_SPEED_FREQ_LOW,
	GPIO_NOPULL,
	GPIO_AF2_TIM2};
	
	HAL_GPIO_Init(GPIOB, &initStrPWM);
	
	TIM2->PSC = 799;
	TIM2->ARR = 200;
	
	TIM2->CCMR1 &= ~TIM_CCMR1_CC2S; 
	TIM2->CCMR1 |= (6 << TIM_CCMR1_OC2M_Pos); 
	TIM2->CCMR1 |= TIM_CCMR1_OC2PE; 
	TIM2->CCER |= TIM_CCER_CC2E; 
}

// Angle ranges from 0 to 16 "ticks"
void servoUtil_setServo(uint8_t angle) {	
	TIM2->CR1 &= ~TIM_CR1_CEN; // Disable Timer
	
	if (angle < 0 || angle > 16) {
		return;
	}
	TIM2->CCR2 = 6 + angle; // Set the duty cycle to be between 3 and 11 %
	
	TIM2->CR1 |= TIM_CR1_CEN; // Enable Timer
}

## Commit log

2024-04-05 enable/disable timer in playTune
2024-04-05 attempt at PWM signaling
2024-04-05 UART for debug
2024-04-05 Updated registers, still not working
    [main.c]
2024-04-10 Attempt to change UART pins
2024-04-10 PWM working on PC6
2024-04-10 USART working but not ADC
2024-04-11 PWM moved to PB5
2024-04-14 Fix UART on pin C10 and C11
    [main.c]
2024-04-14 Starting work on DMA implementation
2024-04-15 try to connect to accelerometer
2024-04-17 Fix knock pattern detection bugs
    [main.c]
2024-04-18 read accelerometer
2024-04-22 DMA reading from two channels, channel 2 not working
    [main.c]
2024-04-23 DMA reading from two channels, PC0 and PC5
2024-04-23 Updated doPuzzle2
    Added stub code for puzzle 2. Requires implementation of LED enablers as well as getOrientation function
2024-04-23 doPuzzle2 and LED config
    Added accelerometer reading to doPuzzle2() as well as LED configuration and toggle for pins PA8 to PA13
2024-04-23 disabled accel test code
    commented out the accel test code within main running loop, re-enabled the switch logic
2024-04-24 remove pin A13
2024-04-24 Switch to PB3 for servo
2024-04-24 add pin 15
2024-04-24 Add STL models for the box
    [Puzzle Box Lid.stl, Puzzle Box.stl]
2024-04-24 Updated to 4 channels on ADC
2024-04-24 Implement doPuzzle3
    Progress on doPuzzle3 as well as a function to make box side LEDs flash, to indicate progress
2024-04-24 Updated doPuzzle3
    Added configurable threshold value for resistor checks. Established buffer value meanings (see comment above dmaUtil_buffer)
2024-04-24 Implemented doGameEnd
    implementation of doGameEnd, as well as locking/unlocking the servo at the start/end.
2024-04-25 Changing ADC channels
2024-04-25 Replace LED initialization with HAL
    [main.c]
2024-05-06 Pins update & solution added
    Added finalized pin configuration used in Demo-day. Also added a fun hints section, as well as the solution for the box.

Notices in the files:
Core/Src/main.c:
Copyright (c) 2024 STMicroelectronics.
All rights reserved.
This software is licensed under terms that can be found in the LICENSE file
